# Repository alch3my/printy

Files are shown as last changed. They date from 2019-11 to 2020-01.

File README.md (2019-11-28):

# Printy

Printy is an Open Source SLA 3D printer. 
Visit us at www.alch3my.com

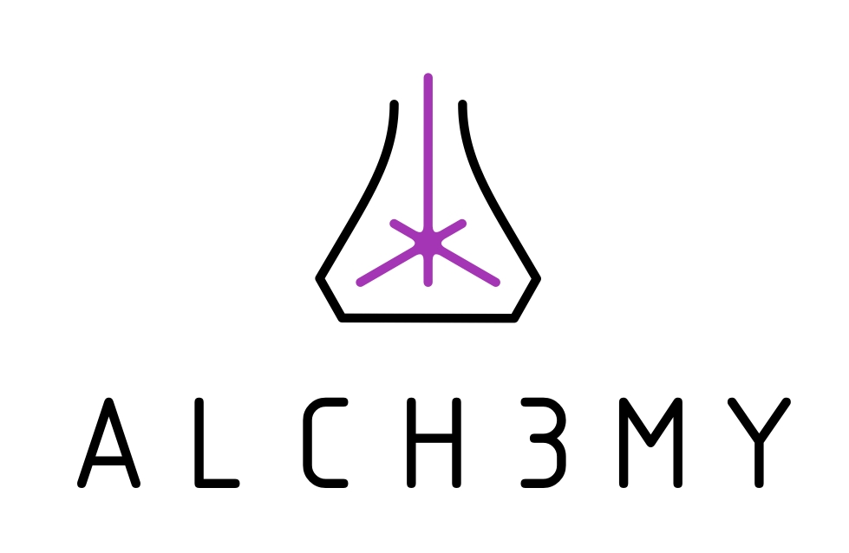
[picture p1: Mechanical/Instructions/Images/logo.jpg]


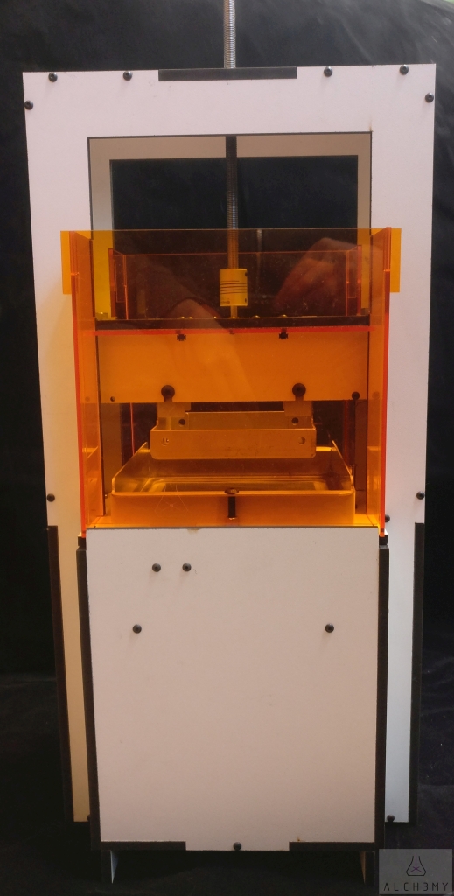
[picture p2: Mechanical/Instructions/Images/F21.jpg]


## Description
Alch3my is an open-source initiative for making the latest 3D printing technology accessible to everyone. Printy is an open-source SLA printer. We aim to democratize SLA technology with this fun and easy to build kit. Assembly takes 4 hours.

## Sourcing the Components
### Option 1: Everything from Alch3my
Purchase a complete kit. This takes all the work out of qualifying and sourcing. This option is perfect for a weekend project.
### Option 2: Only the Essentials
Do you have access to a laser cutter? Do you already have Arduino Mega, NEMA17 motor, stepper board, switches, etc from other projects? We will provide an essentials kit that includes Alch3my created hardware: the ResinShield and the aluminum sheet metal pieces. Download bill of materials and all the laser cutting DXF files from our website or GitHub account.
### Option 3: From Scratch
Are you a hard core maker? Do you like to make, improve, and redistribute hardware? We will provide schematics, gerbers, firmware, CAD files and documentation at Alch3my.com or our GitHub page so you can base your next design on ours. Please observe the license and give credit to Alch3my.

## [Build Instructions](./Mechanical/Instructions/BuildInstructions.md)

## [Software Installation](http://www.alch3my.com)

## [Calibration](http://www.alch3my.com)

Plans published by Alch3my LLC.

CERN OHL v1.2 license whenever appliable.

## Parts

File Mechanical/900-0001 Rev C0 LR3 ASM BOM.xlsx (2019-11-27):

Main Product
Item # | Name | Quantity | Comment | Part # | Supplier | Additional Info
1 | Laser cut pieces | 1 |  | 200-0001 Rev C0 | Ponoko
2 | Aluminum print bed | 1 | With 95185A640 pressed | 201-0001 Rev C
3 | Resinshield | 1 | Contact Alice (alice-yi@elecrow.com) | 101-0001 Rev G | Elecrow | reference number 104645
4 | Laser | 1 | 405nm 50mW, without driver, contact Merry Young (sales@laserland.com) | 3350 405nm 50mW | laserland.com |  | https://store.laserland.com/diode-laser-module/405nm/405dot/3350-405d.html
5 | Galvo + driver | 1 | HT-15K
6 | Stepper driver | 1 | Common open source part (A4988), must have heatsink
7 | Arduino Mega | 1 | Common open source part, any equivalent will work
8 | endstop switch | 3 | Common open source part, any equivalent will work
9 | 12v 3A regulated wall supply | 1 | arduino size barrel
10 | 3 pin JST cable | 1 | Source from galvo manufacturer
11 | 3 pin power cable | 1 | Source from galvo manufacturer
12 | Aluminum resevoir | 1 |  | 201-0002 Rev A3
13 | FEP film | 1 | 5mil thick, 8inx8in, also source from CS Hyde | 85905K66 |  | https://www.mcmaster.com/85905k66
14 | NEMA17 | 1 | 1.5A, 1M cable, 1.8deg, 0.1in female connector for headers
15 | Fastener Kit | 1 |  | 202-0001 Rev C
16 | Mechanical Kit | 1 |  | 202-0002 Rev A
17 | Misc Kit | 1 |  | 202-0003 Rev C
Misc Kit | 202-0003 Rev C
Item # | Name | Quantity | Comment | Part # | Supplier | Additional Info
1 | Adhesive zip tie mount | 4 | Higher quantity package is OK if cheaper |  |  | https://www.mcmaster.com/7566k25
2 | Double sided tape | 1 | 3M VHB RP32, 0.75in width, >= 36inch cut strip or roll | RP32 | 3M
3 | Zip tie | 10 | 0.1" wide >= 3" long. Higher quantity package is OK if cheaper | 7130K12 | mcmaster | https://www.mcmaster.com/7130k12
4 | Wire loom | 1 | 2ft
5 | Laser safety goggles | 1 | Must block 405nm
6 | Single sided tape | 1 | Polyester tape, 3M 1318-1 or equivalent, 0.75in width, >= 36in strip or roll |  | 3M
7 | Metric allen wrench set | 1 | Must include M2, M2.5, M3. Keep cost <$0.50
Mechanical | 202-0002 Rev A |  | Try to source all from the same vendor
Item # | Name | Quantity | Comment | Part # | Supplier | Additional Info
1 | ACME T8x1 200mm with cart | 1 | T8, ACME, 1mm pitch, 200mm long, 8mm diameter, cart must have exact bolt pattern
2 | LMK8LUU | 2 | Pay attention to height, should be around 45mm
3 | SHF8 | 2
4 | Linear rail 8mm 300mm/12in | 2 | 8mm diameter, 300mm/12in long, pay attention to end machining
5 | 5mm to 8mm coupler | 1
Fasteners | 202-0001 Rev C
Item # | Name | Quantity | Comment | Part # | Supplier 1 | Additional Info
1 | M5x20 screw | 10 |  | 91239A233 | mcmaster | https://www.mcmaster.com/91239a233
2 | M4x10 screw | 3 |  | 91239A144 | mcmaster | https://www.mcmaster.com/#91239a144/=1502lqc
3 | M3 nut | 100 |  | 98676A100 | mcmaster | https://www.mcmaster.com/#98676a100/=1502cdh
4 | M3 brass press fit nut | 25 |  | 94510A240 | mcmaster | https://www.mcmaster.com/#94510a240/=1502d99
5 | M3x14 screw | 100 |  | 91239A118 | mcmaster | https://www.mcmaster.com/#91239A118
6 | M3x10 screw | 10 |  | 91239A115 | mcmaster | https://www.mcmaster.com/#91239a115/=1502ox1
7 | M3x16 screw | 8 |  | 91239A120 | mcmaster | https://www.mcmaster.com/#91239A120
8 | M3x50 screw | 1 |  | 92125A151 | mcmaster | https://www.mcmaster.com/92125a151
9 | M5 nut | 10 |  | 90592A095 | mcmaster | https://www.mcmaster.com/90592a095
10 | M5 standoff | 2 |  | 98952A141 | mcmaster | https://www.mcmaster.com/98952a141

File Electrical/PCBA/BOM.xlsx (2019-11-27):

 | RefDes | Name | Value | Description | Quantity | Pattern | Manufacturer | MPN
Fitted | C101, C102, C104, C108, C110, C113, C117, C118, C208, C209 | CAP_0805 | 10u | CAP CER 10UF 25V X5R 0805 | 10 | CAP_0805 |  | GRM21BR61E106KA73K | 96
Fitted | C103, C105, C112, C114, C115, C116, C202, C206, C207, C210, C301, C401 | CAP_0805 | 1u | CAP CER 1UF 35V X5R 0805 | 12 | CAP_0805 |  | GRM219R7YA105MA12D | 19
Fitted | C106, C109, C201, C203, C204, C205 | CAP_0603 | 100p | CAP CER 100PF 50V C0G/NP0 0603 | 6 | CAP_0603 |  | C0805C101J5GACTU
Fitted | C107, C111 | CAP_0603 | 6.8n | CAP CER 6800PF 50V C0G/NP0 0603 | 2 | CAP_0603 |  | CL21B682KBANNNC
Fitted | C302, C303 | CAP_1210 | 22u | CAP CER 22UF 16V X5R 1210 | 2 | CAP_1210 |  | CL32A226MOJNNNE
Not-fitted | C402, C502 | CAP_0805 | opt |  | 2 | CAP_0805
Not-fitted | C501 | CAP_1210 | opt |  | 1 | CAP_1210
Fitted | D101, D104 | PMEG4020ETP |  |  | 2 | SOD-128 | Nexperia | PMEG4020ETP,115
Fitted | D102, D103, D401 | APL3015SRCPRV-F01 |  |  | 3 | APL3015 | Kingbright | APL3015SRCPRV-F01
Not-fitted | D501, D502 | PMEG4020ETP | opt |  | 2 | SOD-128
Fitted | FB101, FB102, FB201, FB301 | BLM18KG221SN1D | 220 @ 100MHz |  | 4 | RES_0603 | Murata | BLM18KG221SN1D
Not-fitted | FD1, FD2, FD3 | Fiducial |  |  | 3 | Fiducial
Fitted | J1, J2, J4, J5, J7, J8 | 644456-8 |  |  | 6 | HDR-1x8T/2.54/20x2 | TE Connectivity | 3-644456-8
Fitted | J3 | 90131-0138 |  |  | 1 | HDR-2x18T/2.54x2.54/46x5 | Molex | 90131-0138
Not-fitted | J6, J9 | 90131-0125 | opt |  | 2 | HDR-2x5T/2.54x2.54/13x5 | Molex | 90131-0125
Not-fitted | J10, J203 | 644456-4 | opt |  | 2 | HDR-1x4T/2.54/10x2 | TE Connectivity | 61300411121
Fitted | J11, J12, J13, J301 | 644456-4 |  |  | 4 | HDR-1x4T/2.54/10x2
Fitted | J101 | 22272031 |  |  | 1 | Molex 3pin | Molex | 0022272031
Not-fitted | J201, J202 | B3B-XH-A | opt |  | 2 | JST B3B-XH-A | JST | B3B-XH-A(LF)(SN)
Fitted | J204 | B3B-XH-A |  |  | 1 | JST B3B-XH-A | JST | B3B-XH-A(LF)(SN)
Fitted | J302, J303 | PPTC081LFBN-RC |  |  | 2 | HDR-1x8T/2.54/20x2 | Sullins | PPTC081LFBN-RC
Fitted | J401, J402 | B2B-XH-A |  |  | 2 | JST B2B-XH-A | JST | B2B-XH-A(LF)(SN)
Not-fitted | J501 | OSTVN04A150 | opt |  | 1 | TB-1x4/2.54/11x7/Sc_H | On Shore | OSTVN04A150
Not-fitted | J502 | 644456-2 | opt |  | 1 | HDR-1x2T/2.54/5x2 | TE Connectivity | 3-644456-2
Fitted | Q401, Q402 | 2N7002 |  |  | 2 | SOT23 | Diodes | 2N7002-7-F
Not-fitted | Q501, Q502 | IRLZ44N | opt |  | 2 | TO-220 | Infineon | IRLZ44NPBF
Not-fitted | R1, R302, R304, R305, R306, R307, R501, R502, R503, R504, R505 | RES_0603 | opt |  | 11 | RES_0603
Fitted | R101, R115 | RES_1210 | 0 | RES SMD 0 OHM JUMPER 1/2W 1210 | 2 | RES_1210 |  | CRCW12100000Z0EA
Fitted | R102, R103, R108, R205, R210 | RES_0603 | 49k9 | RES SMD 49.9K OHM 1% 1/10W 0603 | 5 | RES_0603 |  | ERJ-3EKF4992V
Fitted | R104, R106, R112, R113, R202, R203, R204, R206, R207, R208, R209, R211, R401, R403 | RES_0603 | 100k | RES SMD 100K OHM 1% 1/10W 0603 | 14 | RES_0603 |  | AT0603FRE07100KL
Fitted | R105, R114 | RES_0603 | 464k | RES SMD 464K OHM 1% 1/10W 0603 | 2 | RES_0603 |  | RC0603FR-07464KL
Fitted | R107, R111, R402 | RES_0603 | 24k9 | RES SMD 24.9K OHM 1% 1/10W 0603 | 3 | RES_0603 |  | ERJ-3EKF2492V
Fitted | R109, R405 | RES_0603 | 6k04 | RES SMD 6.04K OHM 1% 1/10W 0603 | 2 | RES_0603 |  | ERJ-3EKF6041V
Fitted | R110 | RES_0603 | 53k6 | RES SMD 53.6K OHM 1% 1/10W 0603 | 1 | RES_0603 |  | RC0603FR-0753K6L
Fitted | R201 | RES_0603 | 1k | RES SMD 1K OHM 1% 1/10W 0603 | 1 | RES_0603 |  | ERJ-3EKF1001V
Fitted | R212, R213 | RES_0603 | 24r9 | RES SMD 24.9 OHM 1% 1/10W 0603 | 2 | RES_0603 |  | ERJ-3EKF24R9V
Fitted | R301, R303 | RES_0603 | 0 | RES SMD 0 OHM JUMPER 1/10W 0603 | 2 | RES_0603 |  | ERJ-3GEY0R00V
Fitted | R407 | RES_0603 | 18r2 | RES SMD 18.2 OHM 1% 1/10W 0603 | 1 | RES_0603 |  | ERJ-3EKF18R2V
Fitted | T101, T102 | SRF1260-150M | 15uH |  | 2 | SRF1260 | Bourns | SRF1260-150M
Not-fitted | TP101, TP102, TP103, TP201, TP202, TP203, TP204, TP205, TP206, TP207, TP208, TP501, TP502, TP503 | TESTPOINT |  |  | 14 | Round
Fitted | U101 | LT8582 |  |  | 1 | 4x7DFN | Linear Technology | LT8582EDKD#PBF
Fitted | U102 | NCP1117ST50T3G |  |  | 1 | SOT223-4 | ON Semi | NCP1117ST50T3G
Fitted | U201 | LM4040DIM3-4.1 |  |  | 1 | SOT23 | Texas Instruments | LM4040DIM3-4.1/NOPB
Fitted | U202 | TL084D |  |  | 1 | SOIC-14/150mil | Texas Instruments | TL084CDR
Fitted | U203 | LTC2602CMS8 |  |  | 1 | MSOP-8 | Linear Technology | LTC2622CMS8#PBF
Fitted | U401 | LM321MF |  |  | 1 | SOT23-5 | Texas Instruments | LM321MF/NOPB
Not-fitted | X1 | Arduino Mega |  |  | 1
Not-fitted | X301 | A4988 Carrier |  |  | 1

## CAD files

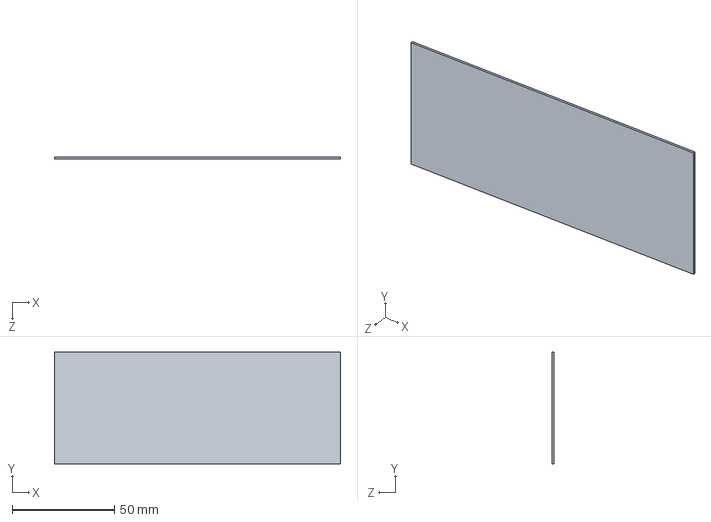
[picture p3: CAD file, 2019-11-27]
Electrical/PCBA/resinshield.step
139.7 x 54.6 x 0.991 mm

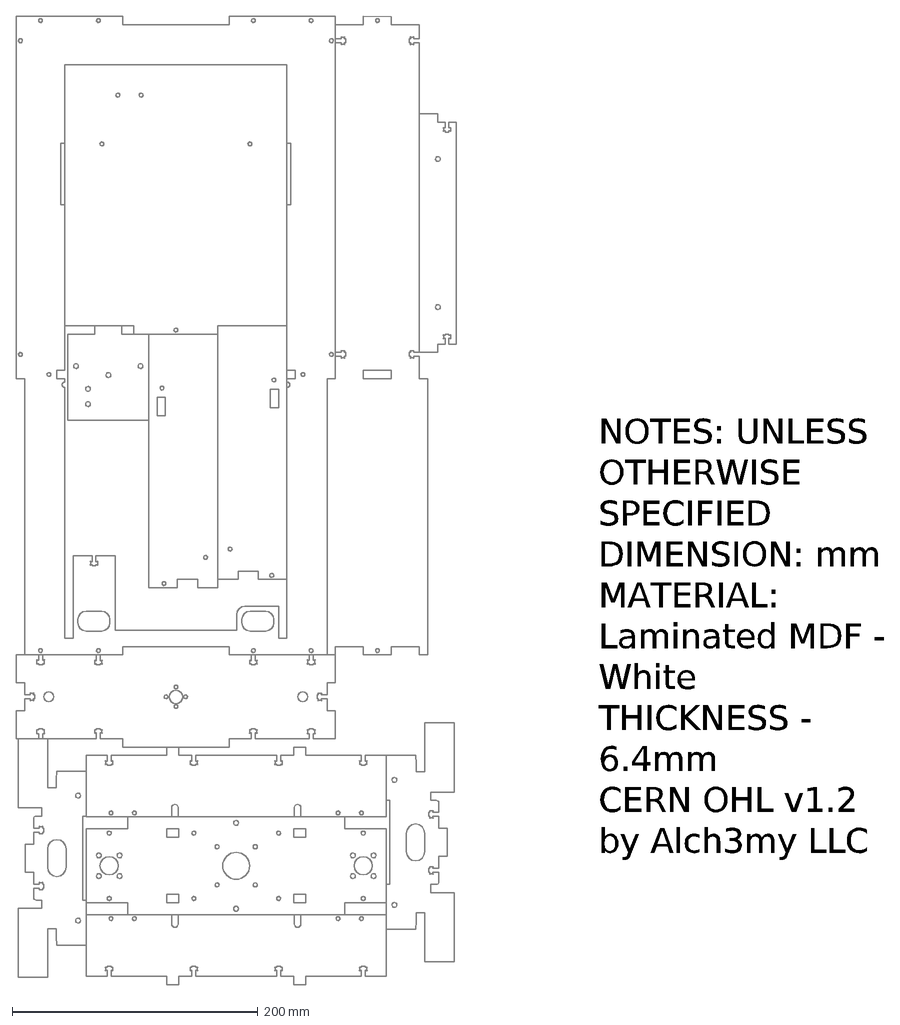
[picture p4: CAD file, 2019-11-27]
Mechanical/200-0001 Laser Cut/wood2_p3.dxf
NOTES: UNLESS OTHERWISE SPECIFIED DIMENSION: mm MATERIAL: Laminated MDF - White THICKNESS - 6.4mm CERN OHL v1.2 by Alch3my LLC

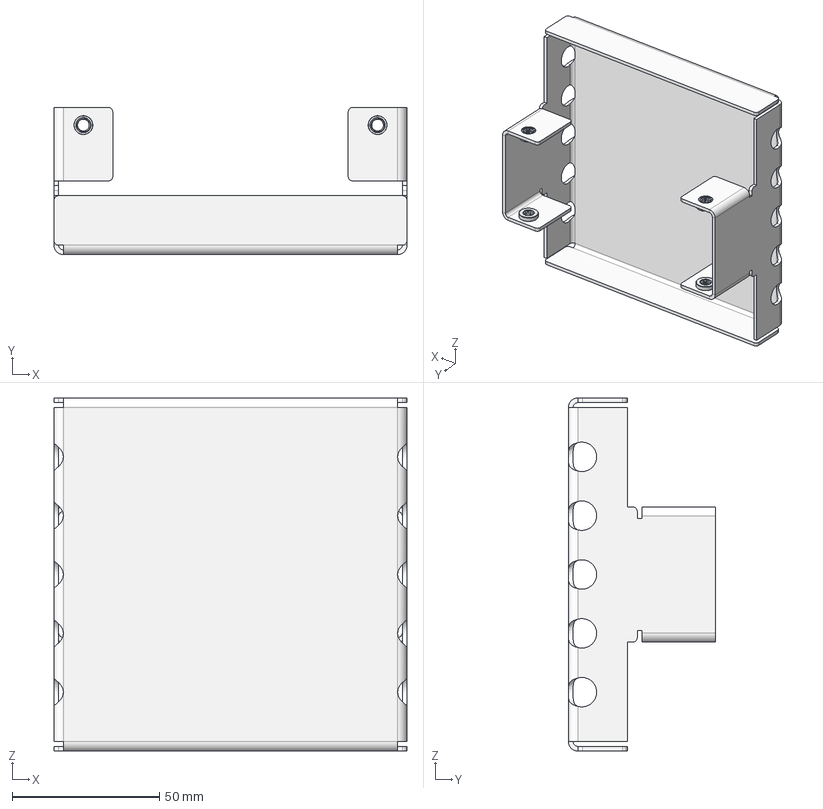
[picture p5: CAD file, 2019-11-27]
Mechanical/201-0001 BedSM/201-0001 Rev C bedsm.stp
120.0 x 50.0 x 120.0 mm
bedsm
95185A640_ZINC-PLTD STL PRESS-FIT NUT FOR SHEET METAL x 4

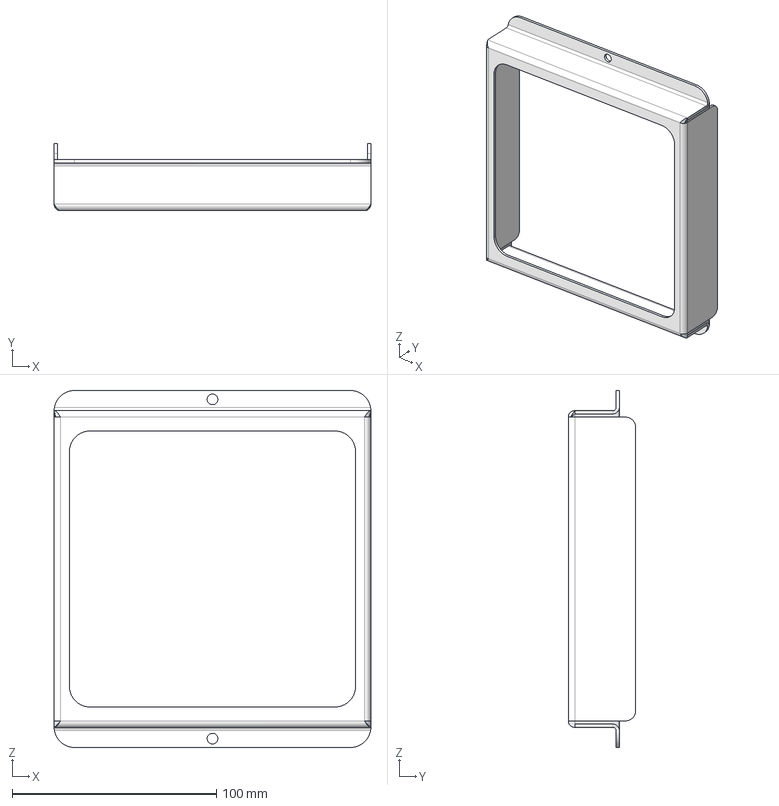
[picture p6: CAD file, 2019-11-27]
Mechanical/201-0002 ReservoirSM/201-0002 Rev A3 reservoirsm.stp
155.0 x 33.0 x 174.7 mm
reservoirsm_weldment_1
reservoirsm

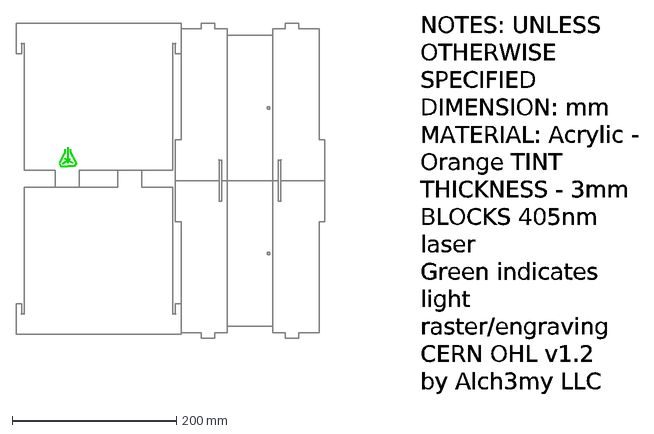
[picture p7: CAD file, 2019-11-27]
Mechanical/200-0001 Laser Cut/clear_orange_p2.dxf
NOTES: UNLESS OTHERWISE SPECIFIED DIMENSION: mm MATERIAL: Acrylic - Orange TINT THICKNESS - 3mm BLOCKS 405nm laser Green indicates light raster/engraving CERN O

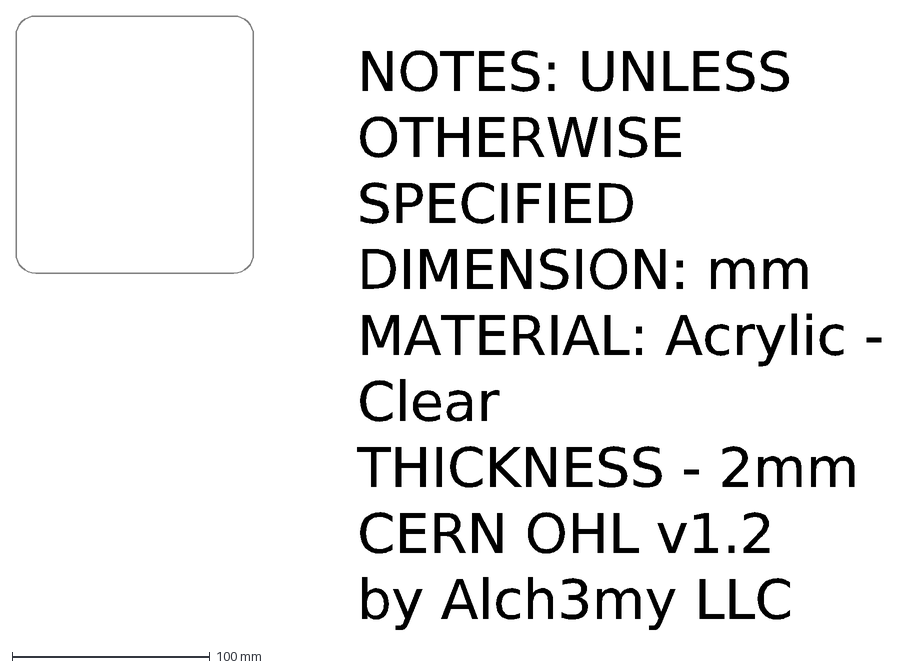
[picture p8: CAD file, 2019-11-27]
Mechanical/200-0001 Laser Cut/clear_acrylic_p1.dxf
NOTES: UNLESS OTHERWISE SPECIFIED DIMENSION: mm MATERIAL: Acrylic - Clear THICKNESS - 2mm CERN OHL v1.2 by Alch3my LLC

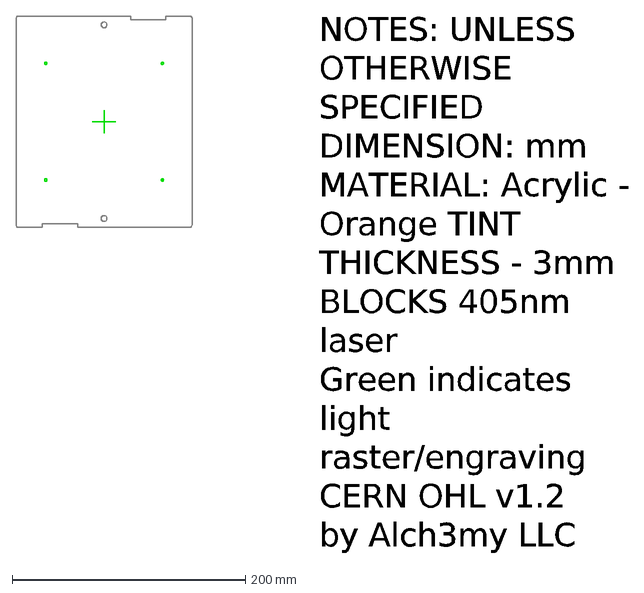
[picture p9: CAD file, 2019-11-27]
Mechanical/200-0001 Laser Cut/clear_orange_p1.dxf
NOTES: UNLESS OTHERWISE SPECIFIED DIMENSION: mm MATERIAL: Acrylic - Orange TINT THICKNESS - 3mm BLOCKS 405nm laser Green indicates light raster/engraving CERN O

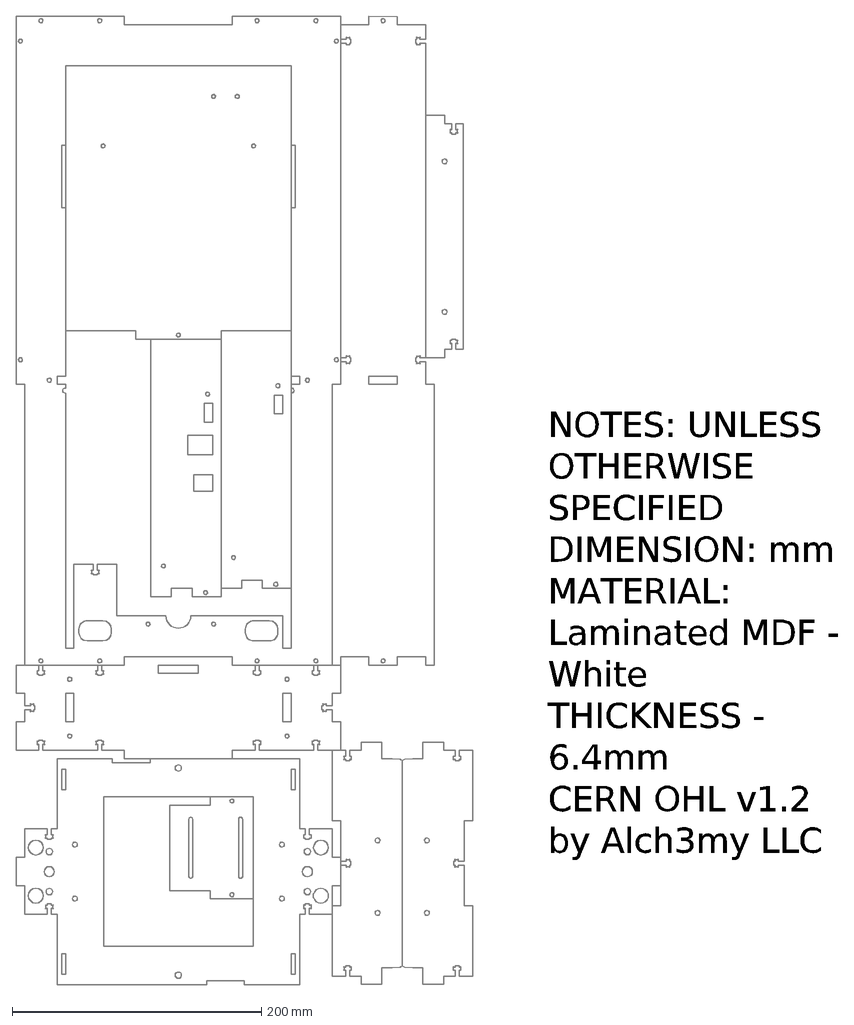
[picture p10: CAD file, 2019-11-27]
Mechanical/200-0001 Laser Cut/wood1_p3.dxf
NOTES: UNLESS OTHERWISE SPECIFIED DIMENSION: mm MATERIAL: Laminated MDF - White THICKNESS - 6.4mm CERN OHL v1.2 by Alch3my LLC

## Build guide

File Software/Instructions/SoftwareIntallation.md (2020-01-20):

# Printy

Printy is an Open Source SLA 3D printer. 
Visit us at www.alch3my.com





## Description
Alch3my is an open-source initiative for making the latest 3D printing technology accessible to everyone. Printy is an open-source SLA printer. We aim to democratize SLA technology with this fun and easy to build kit. Assembly takes 4 hours.

## Software Installation
### Arduino IDE
Get the latest Arduino IDE from https://www.arduino.cc/en/main/software and install.

### Printy Firmware
Get the latest Printy firmware from https://github.com/alch3my/printy/tree/master/Software/Firmware

Connect an Arduino Mega or equivalent microcontroller board via USB to your computer.



Figure F1. Connect Arduino Mega

Load the firmware project "Marlin.ino" into the Arduino IDE

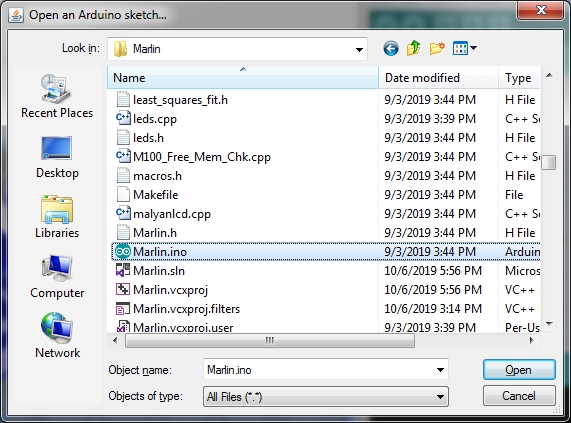
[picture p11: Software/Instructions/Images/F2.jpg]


Figure F2. Load Firmware

Ensure the "board", "processor", and "port" options reflect the connected Arduino Mega or equivalent. Press upload.

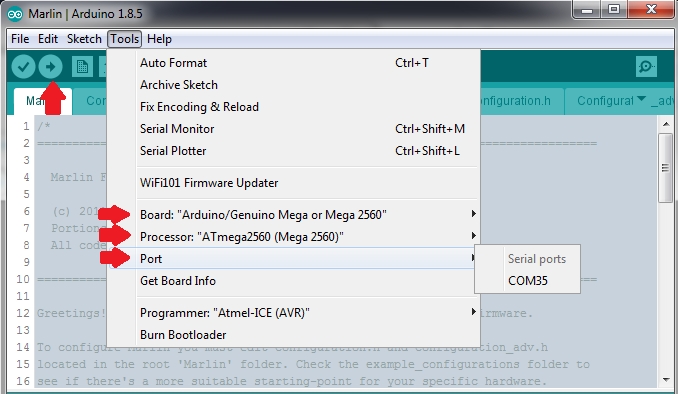
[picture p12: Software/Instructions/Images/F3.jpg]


Figure F3. Arduino IDE Configuration and Upload

Exit Arduino IDE once the upload is successful.

### Repetier Host
Get Repetier Host from https://www.repetier.com and install.

Use the following settings in "Printer Settings" to setup Printy.

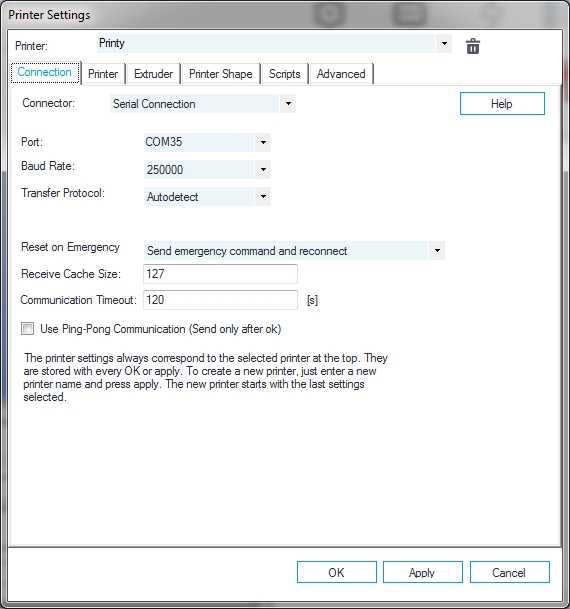
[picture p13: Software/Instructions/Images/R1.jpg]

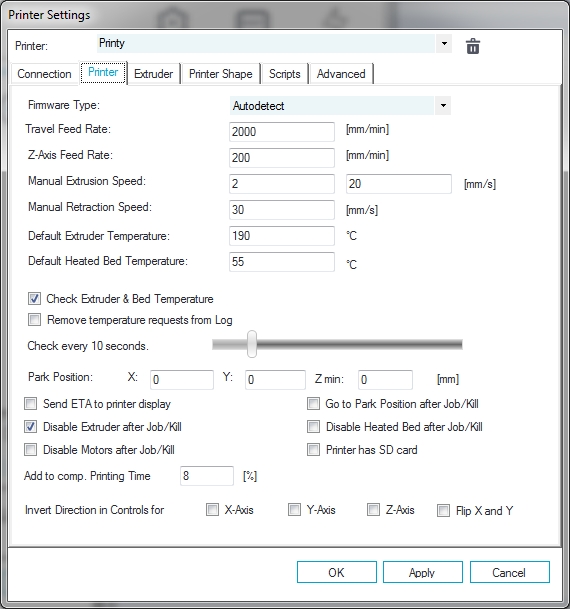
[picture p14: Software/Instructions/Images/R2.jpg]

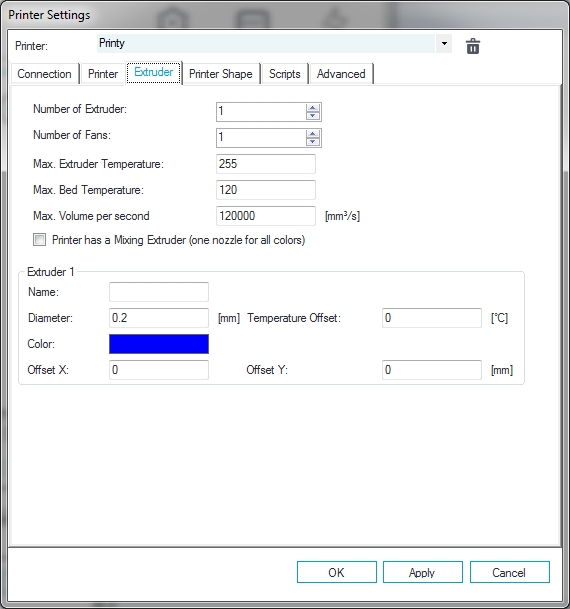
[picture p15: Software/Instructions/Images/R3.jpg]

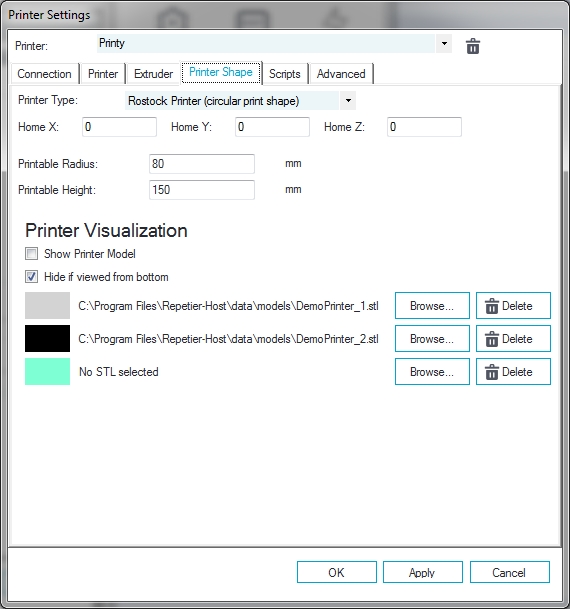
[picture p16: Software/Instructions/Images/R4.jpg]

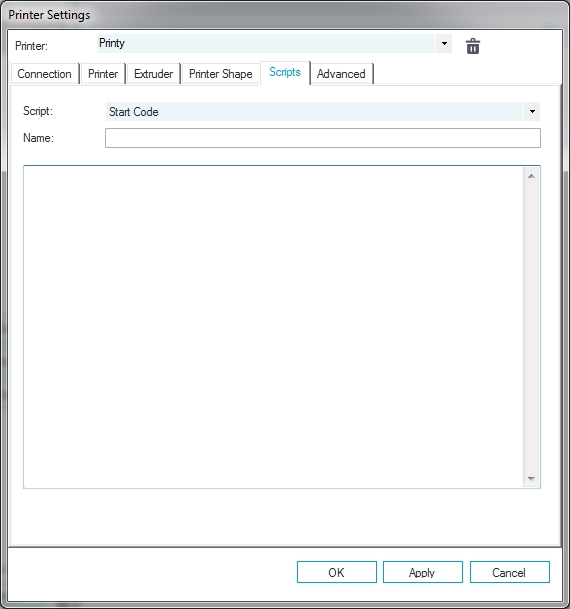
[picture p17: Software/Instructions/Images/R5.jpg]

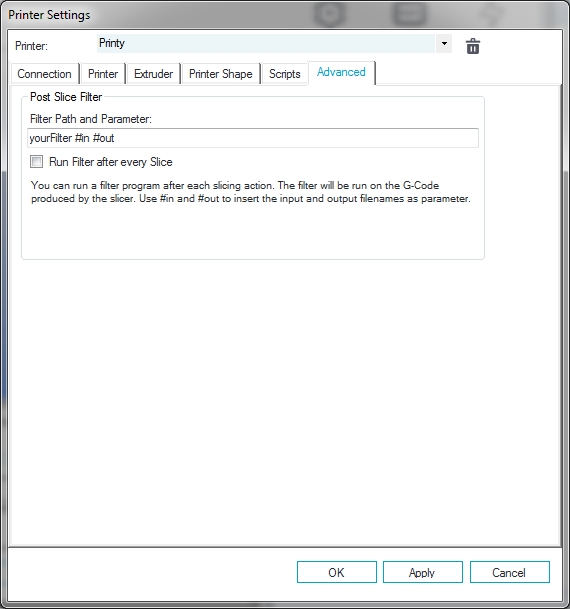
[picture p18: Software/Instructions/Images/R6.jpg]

Figures R1-6. Printer Settings

Note the "Port Number" should be the one your computer assign to the connected Arduino Mega or equivalent microcontroller.

### Slic3r Settings

Slic3r is a slicing tool typically used in FDM printers. Printy mimics the operation of an FDM by steering a laser beam across the print surface. Use the following settings to setup Slic3r. These settings will need to be tweaked for specific resins. Maker Juice G+ was extensively tested with these settings.

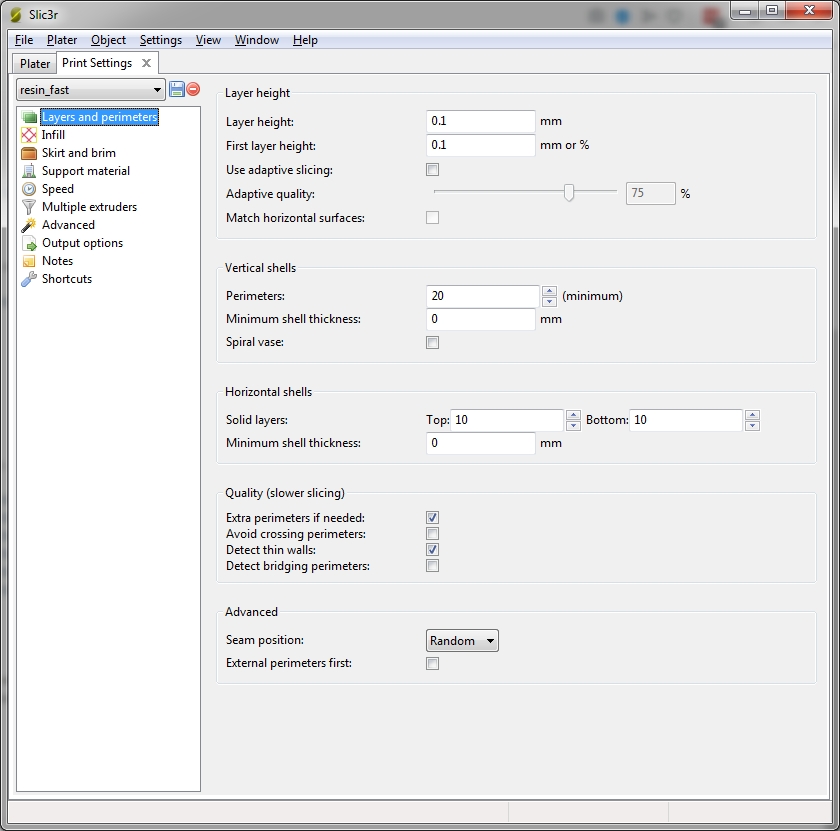
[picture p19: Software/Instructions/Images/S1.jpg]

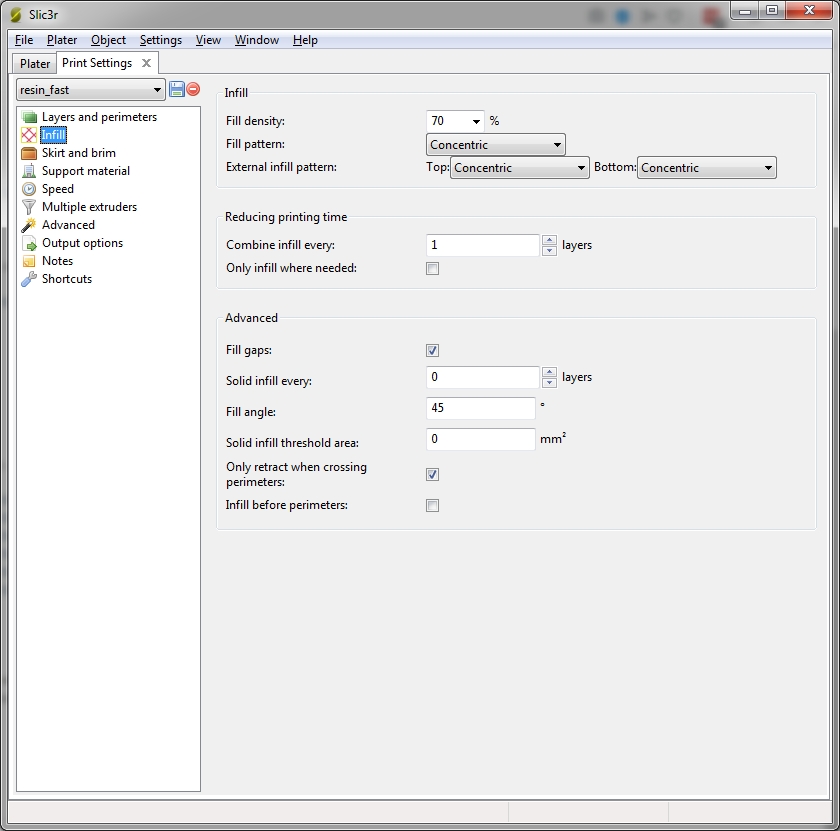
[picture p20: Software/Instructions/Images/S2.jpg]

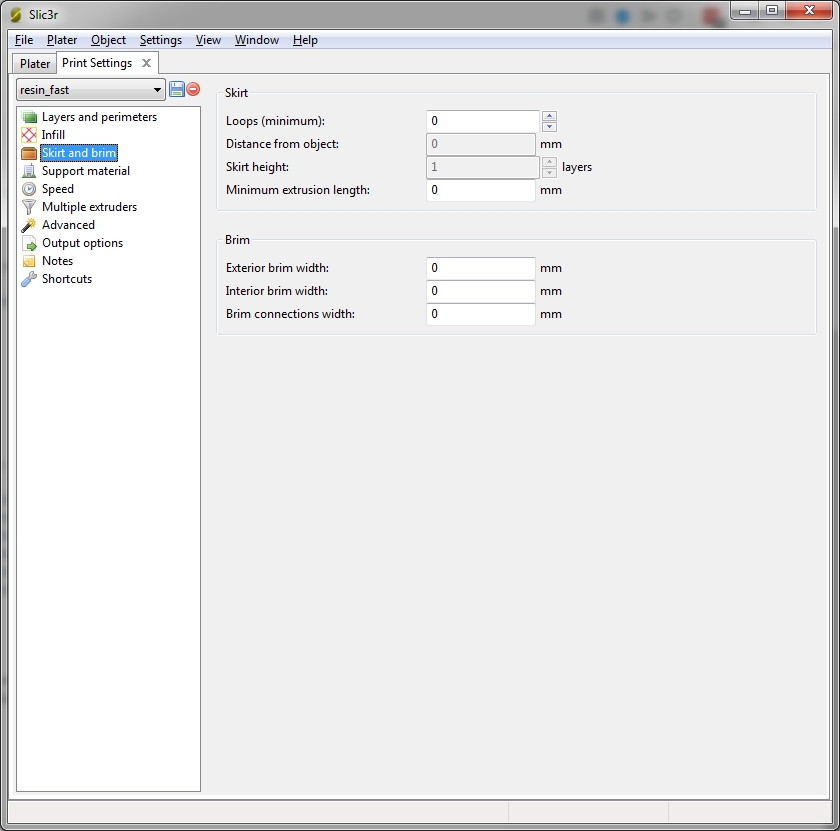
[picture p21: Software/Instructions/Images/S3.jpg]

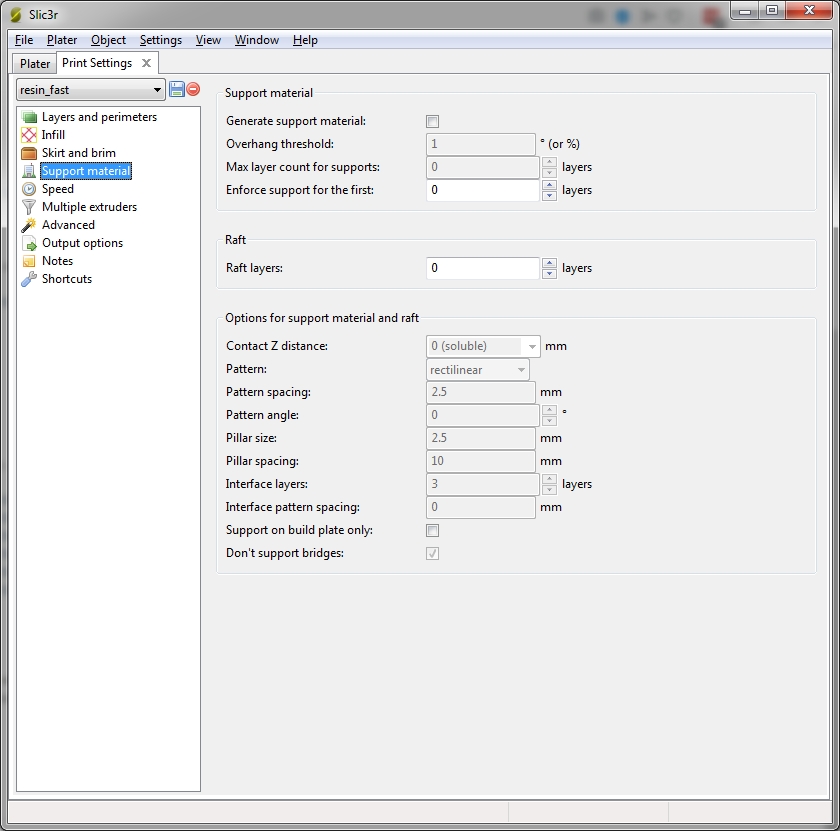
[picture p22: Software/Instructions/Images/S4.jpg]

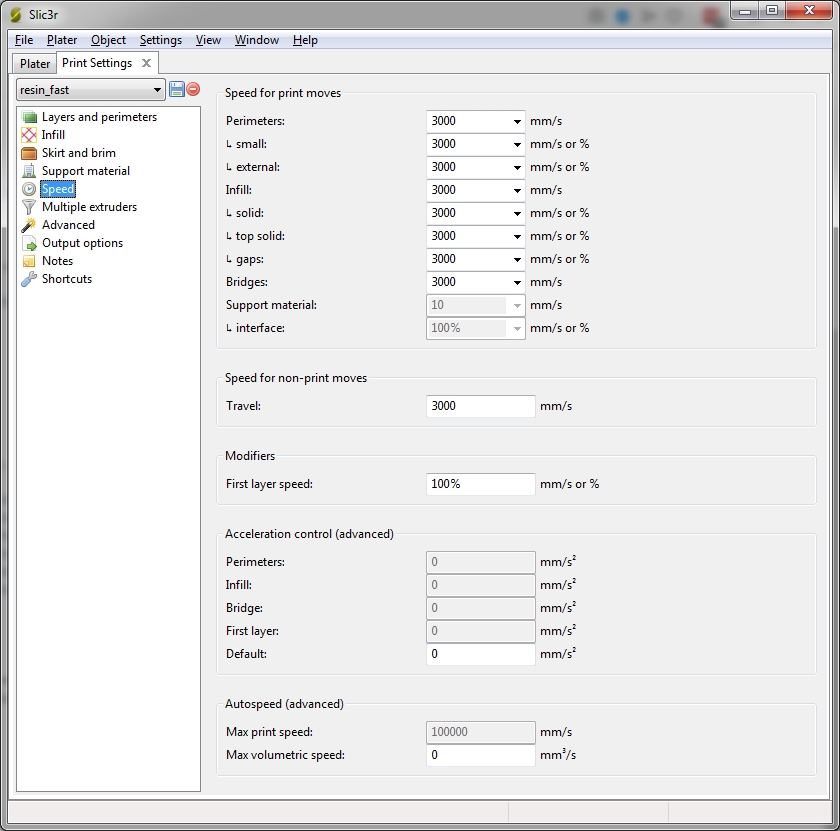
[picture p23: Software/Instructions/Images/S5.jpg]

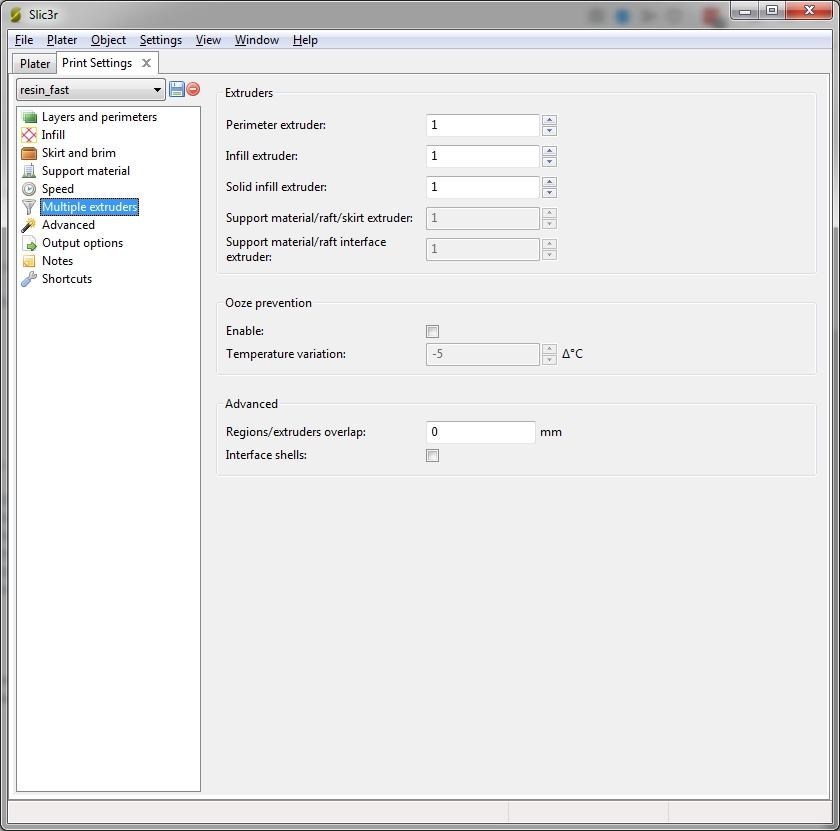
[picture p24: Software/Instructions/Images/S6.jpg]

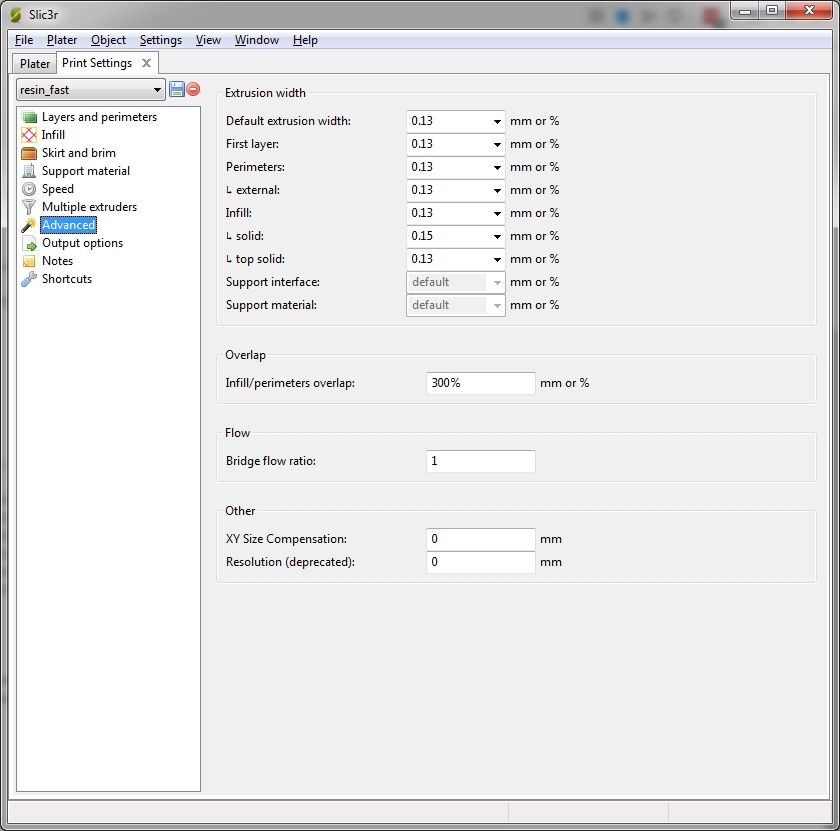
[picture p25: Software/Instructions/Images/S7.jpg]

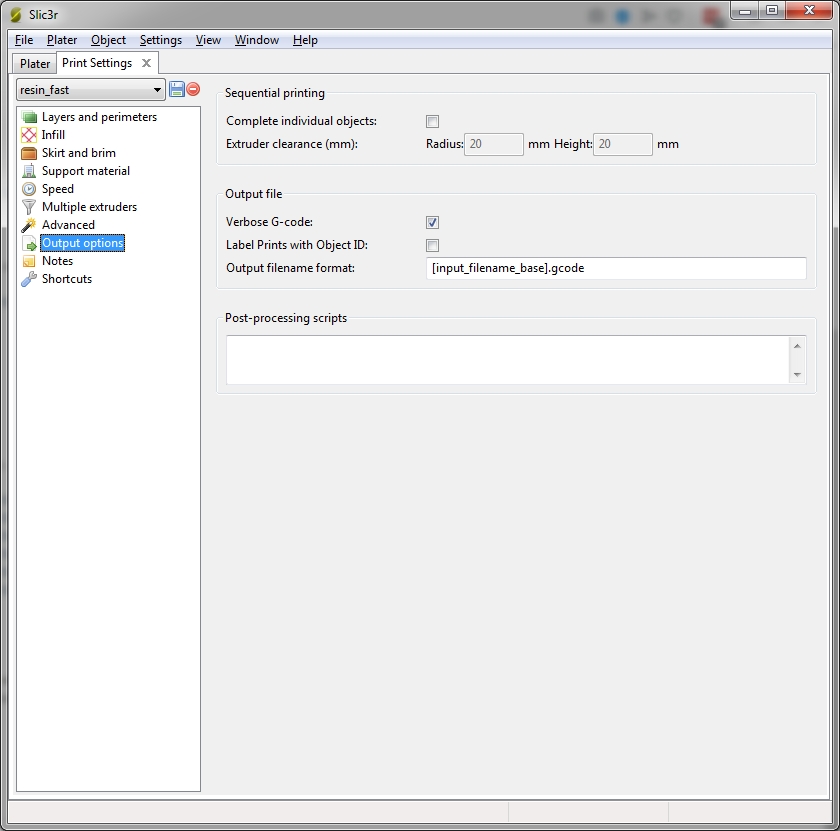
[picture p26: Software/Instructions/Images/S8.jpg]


Figures S1-8. Slic3r Print Setting

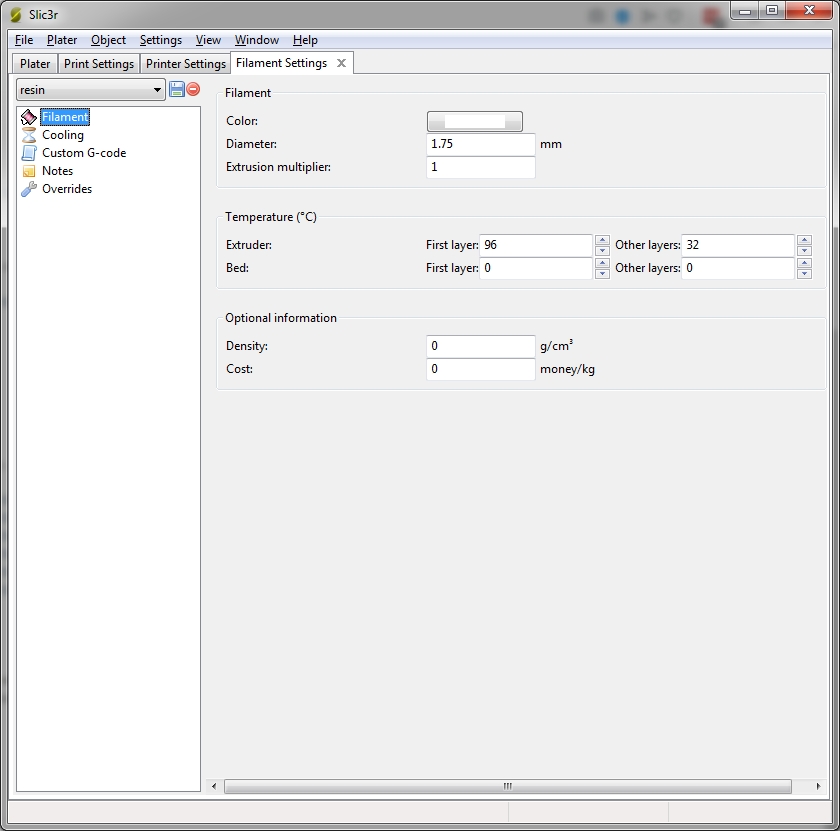
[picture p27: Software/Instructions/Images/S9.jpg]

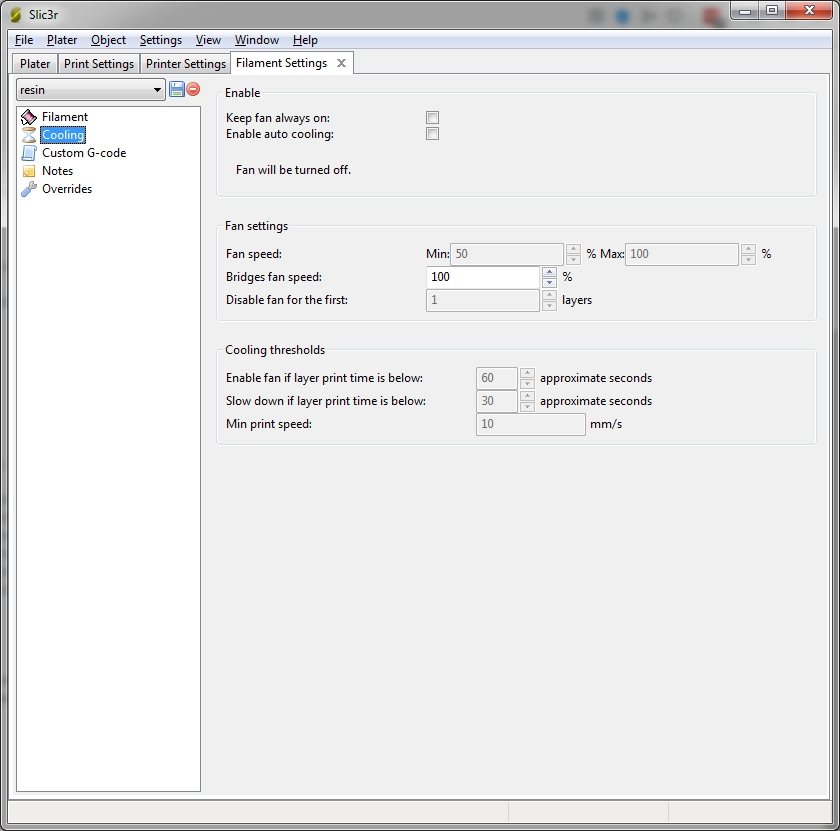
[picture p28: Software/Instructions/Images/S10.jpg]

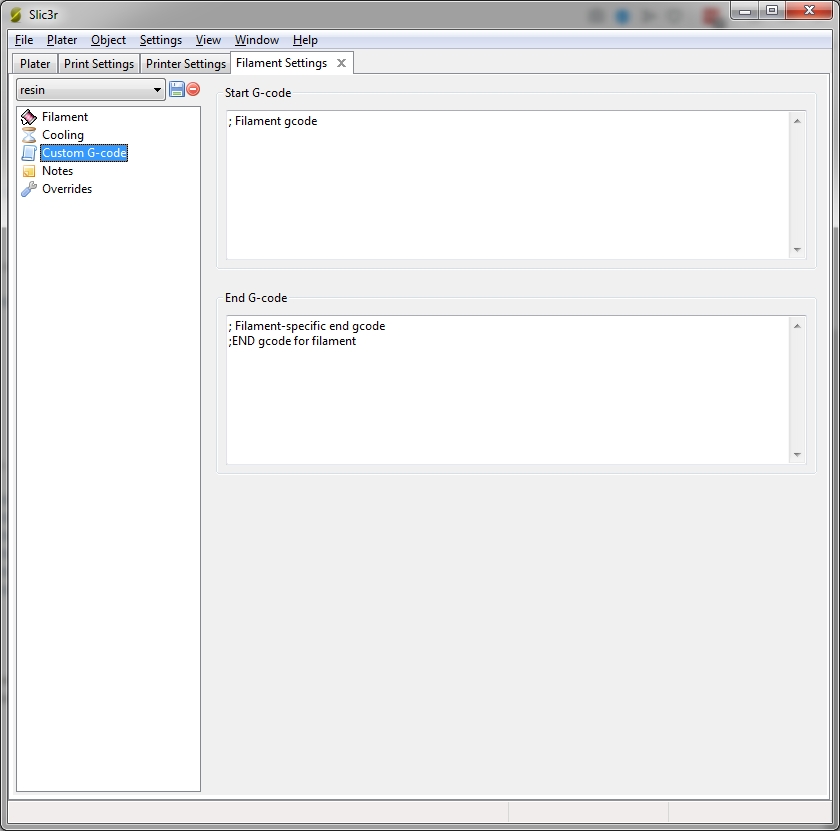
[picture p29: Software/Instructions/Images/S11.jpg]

Figures S9-11. Slic3r Filament Setting

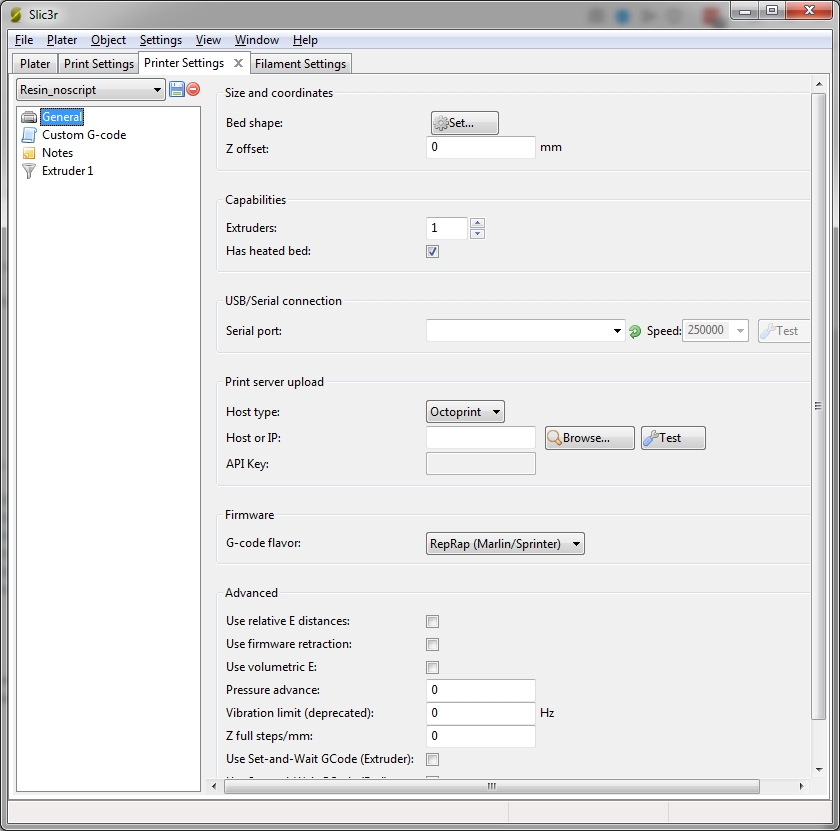
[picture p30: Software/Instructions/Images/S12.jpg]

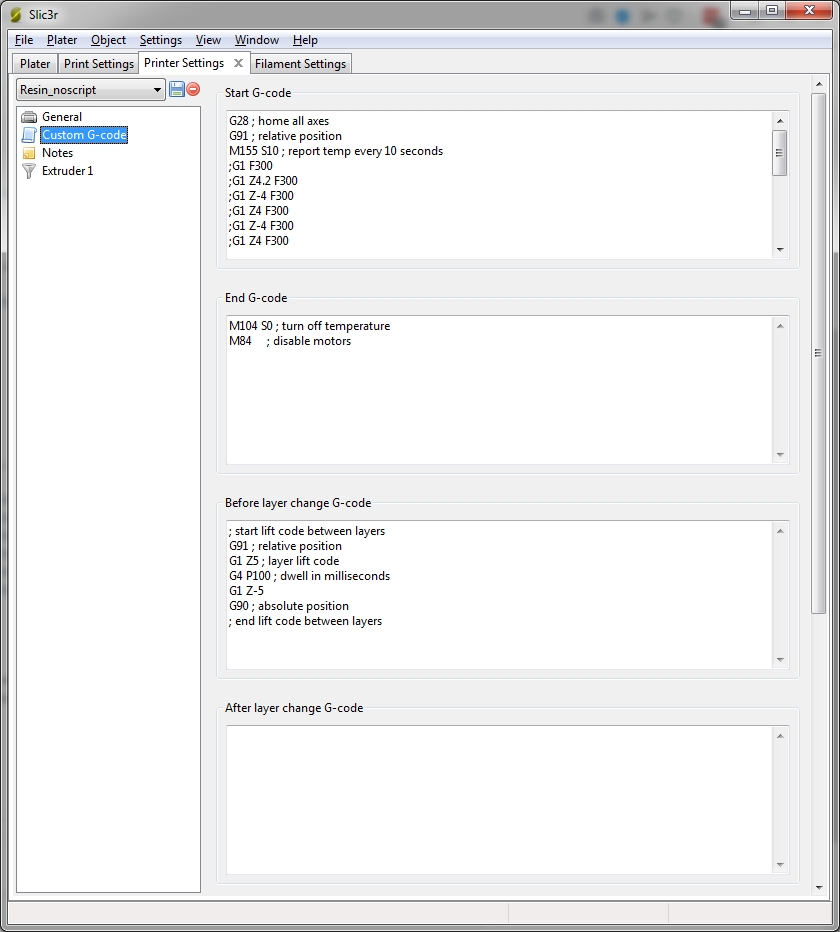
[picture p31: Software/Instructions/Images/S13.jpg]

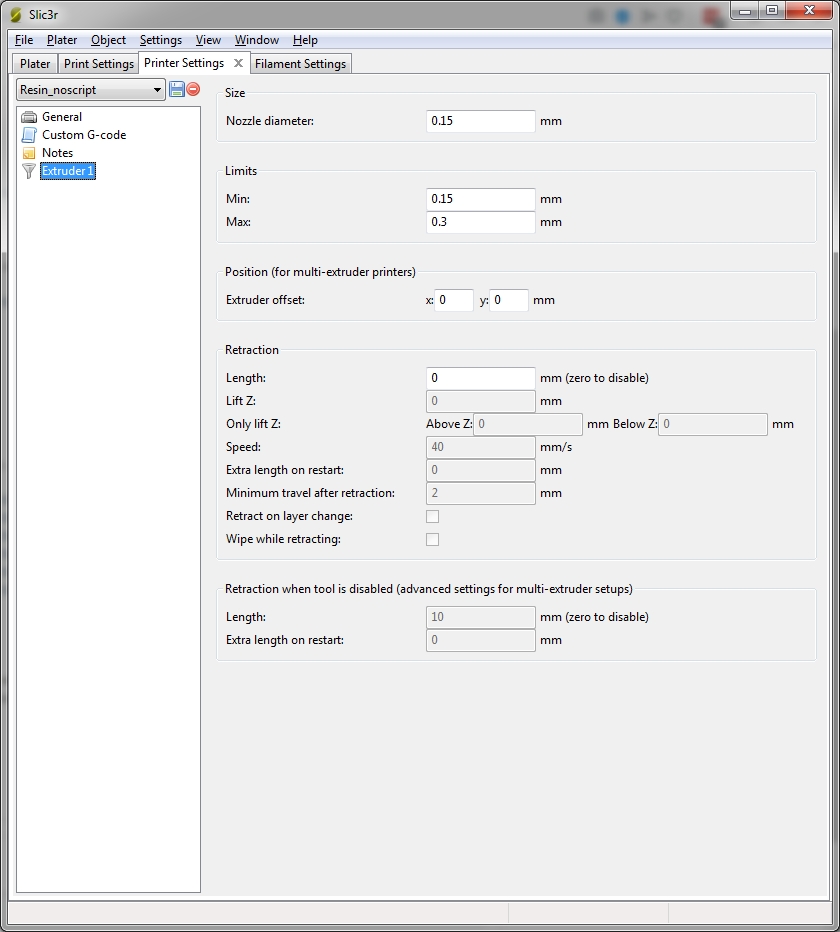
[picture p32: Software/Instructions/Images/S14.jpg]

Figures S12-14. Slic3r Printer Setting

Use the following "Start G-Code" in "Slic3r Printer Setting":

~~~~
G28 ; home all axes
G91 ; relative position
M155 S10 ; report temp every 10 seconds
G1 F300
G1 Z4.2 F300
G1 Z-4 F300
G1 Z4 F300
G1 Z-4 F300
G1 Z4 F300
G1 Z-4 F300
G1 Z4 F300
G1 Z-4 F300
G1 Z4 F300
G1 Z-4.1 F300
G1 Z10 F300
G1 Z-10 F20
G90 ; absolute position
G4 P1000 ; dwell in milliseconds
; end initial lift code
~~~~

Use the following "End G-Code":
~~~~
M104 S0 ; turn off temperature
M84     ; disable motors
~~~~

Use the following "Before Layer Change G-Code":
~~~~
; start lift code between layers
G91 ; relative position
G1 Z5 ; layer lift code
G4 P100 ; dwell in milliseconds
G1 Z-5
G90 ; absolute position
; end lift code between layers
~~~~

### Published by Alch3my LLC 

### CERN OHL v1.2 license whenever applicable.

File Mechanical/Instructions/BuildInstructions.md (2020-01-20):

# Printy Build Instructions





## Description
Alch3my is an open-source initiative for making the latest 3D printing technology accessible to everyone. Printy is an open-source SLA printer. We aim to democratize SLA technology with this fun and easy to build kit. Assembly takes 4 hours.

## Sourcing the Components
### Option 1: Everything from Alch3my
Purchase a complete kit. This takes all the work out of qualifying and sourcing. This option is perfect for a weekend project.
### Option 2: Only the Essentials
Do you have access to a laser cutter? Do you already have Arduino Mega, NEMA17 motor, stepper board, switches, etc from other projects? We will provide an essentials kit that includes Alch3my created hardware: the ResinShield and the aluminum sheet metal pieces. Download bill of materials and all the laser cutting DXF files from our website or GitHub account.
### Option 3: From Scratch
Are you a hard core maker? Do you like to make, improve, and redistribute hardware? We will provide schematics, gerbers, firmware, CAD files and documentation at Alch3my.com or our GitHub page so you can base your next design on ours. Please observe the license and give credit to Alch3my.

## Build Instructions
### Overview
The Printy kit contains many laser cut pieces. Pay close attention to the orientation of pieces, since some of the pieces only fit together in the orientations described. All orientation directions assumes the printer is facing you. The __front__ is the side closest to you.; __left__ is on your left hand side, etc.
#### Setup
Begin by spreading all the pieces out for easy identification and to ensure you have all the necessary pieces. Please refer to the Bill of Materials (BOM).
#### Tools Needed
Metric Allen wrenchs including 2mm, 2.5mm, 3mm. A small wrench. Clear tape. Rough sand paper (20-40 grit).
#### Spares
Ample spare screws and nuts are shipped with the kit. If more are needed, refer to the BOM for hardware specifications.
#### Peel
Peel the protective tape from all laser cut pieces.

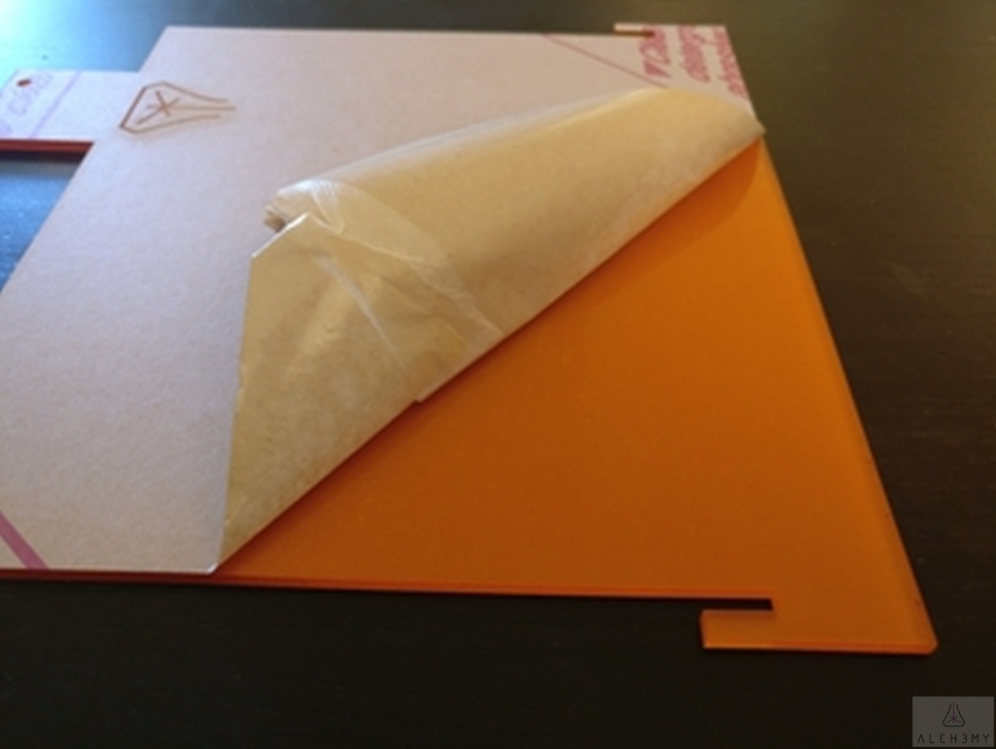
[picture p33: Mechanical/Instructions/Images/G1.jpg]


Figure G1. Peel the Protective Tape

#### T-Slot Joints
Printy is held together by T-slot joints. A bolt is inserted through one interface and a nut is inserted into a slot on the receiving end. __Do not overtighten!__

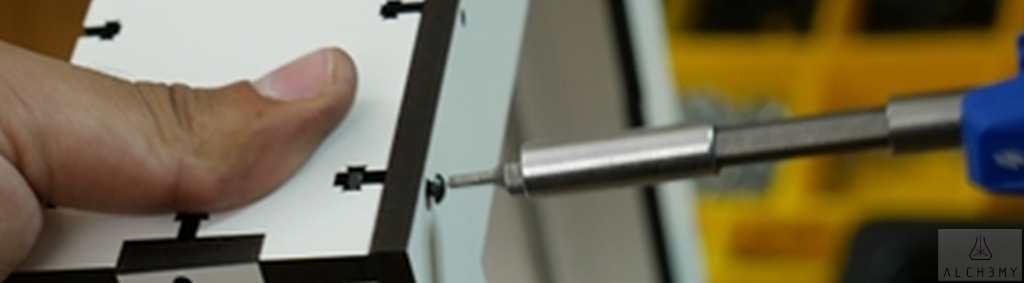
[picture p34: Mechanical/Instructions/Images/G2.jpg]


Figure G2. Proper Installation for T-Slot Joint

### Building the Crane
The crane holds the print platform, all holes are symmetric for your convenience. The two holes are for attaching the endstop switch, use the holes on the __front-right__.

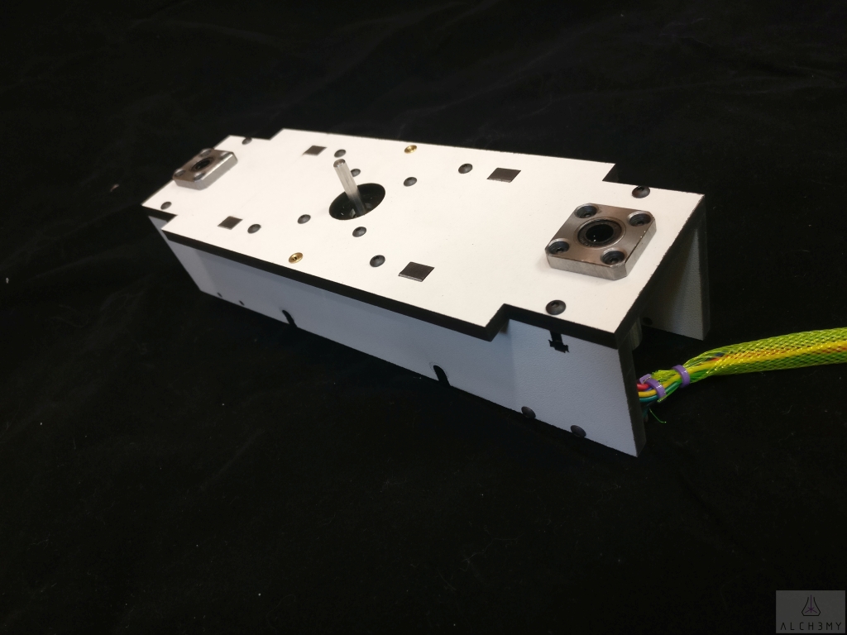
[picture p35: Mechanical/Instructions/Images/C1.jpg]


Figure C1. Assembly Orientation for the Crane

Attach the front and back piece of the crane to the top of the crane with 4 M3 nuts and 4 M3x14 screws each. A total of 8 M3 nuts and 8 M3x14 screws will be used.

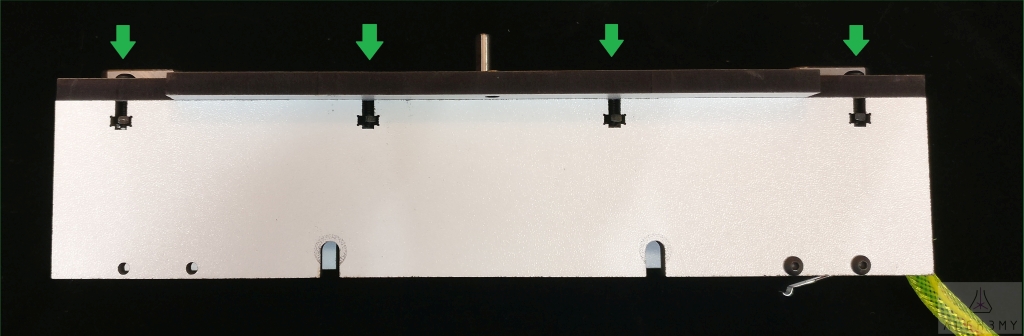
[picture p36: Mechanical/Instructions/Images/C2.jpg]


Figure C2. Assemble the Crane

Attach the NEMA17 motor to top of the crane with 4 M3x10 screws. Wires should come out on the __right__ side.

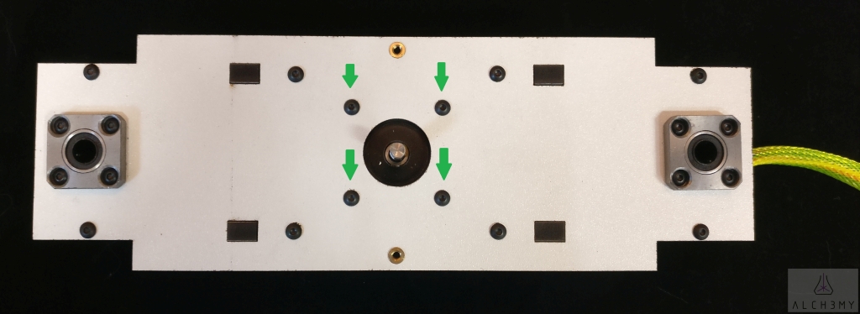
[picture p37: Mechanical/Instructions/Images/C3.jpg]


Figure C3. Install NEMA 17 Motor

Press in 8 M3 brass press-fit nuts into the crane from the __bottom__, 2 more from the __top__

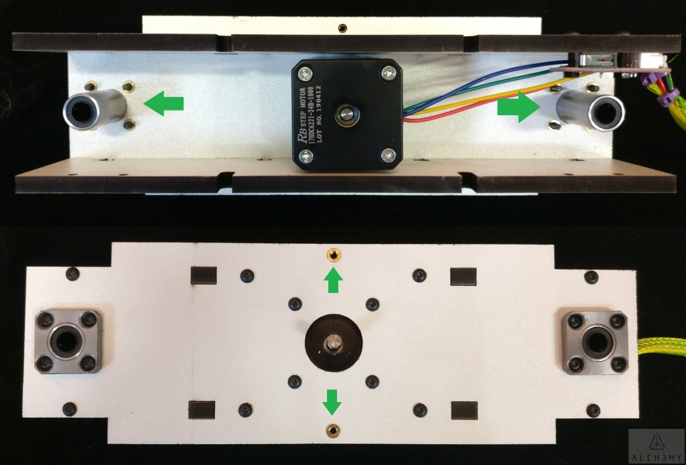
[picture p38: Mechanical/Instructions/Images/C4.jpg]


Figure C4. Brass Press-Fit Nuts

Insert the LMK8LUU bearings through top of the crane and attach with 4 M3x14 screws.

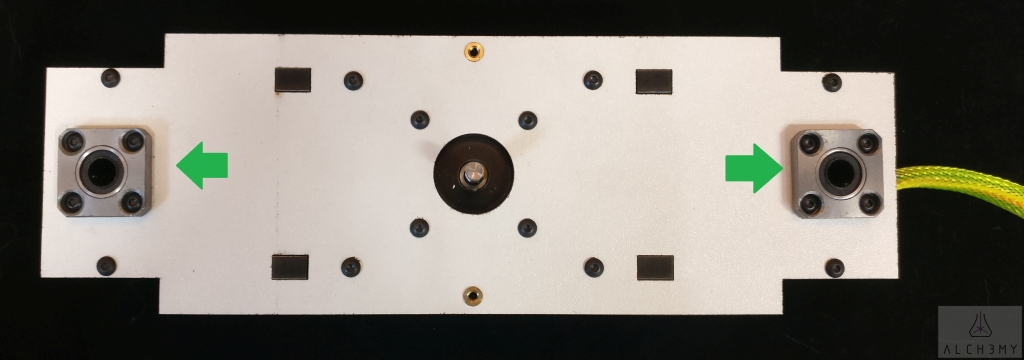
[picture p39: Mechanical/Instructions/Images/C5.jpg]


Figure C5. LMK8LUU Bearings

Attach the endstop switch with 2 M3x16 screw and 2 M3 nuts. The wires should points towards the __right__ side.

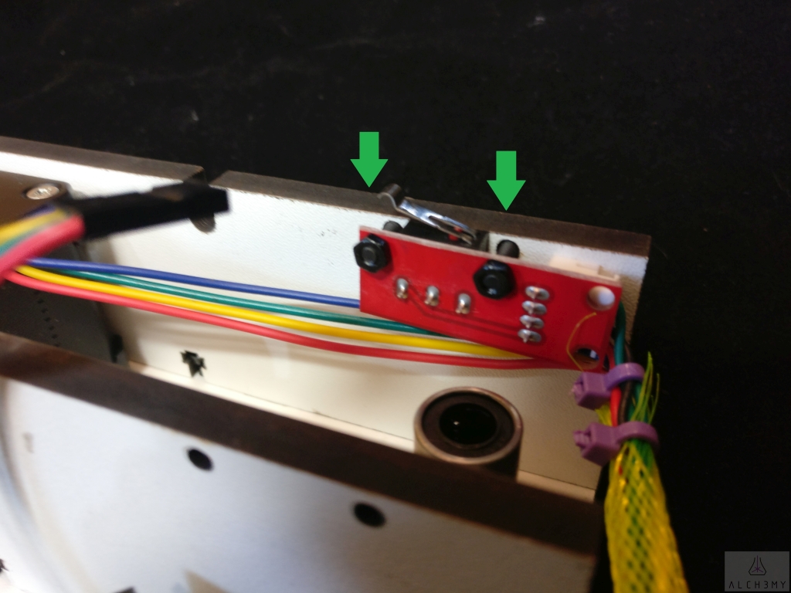
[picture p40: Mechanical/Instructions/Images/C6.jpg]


Figure C6. Endstop Switch

Enclose the motor and endstop wires in a sleeve, zip tie the ends

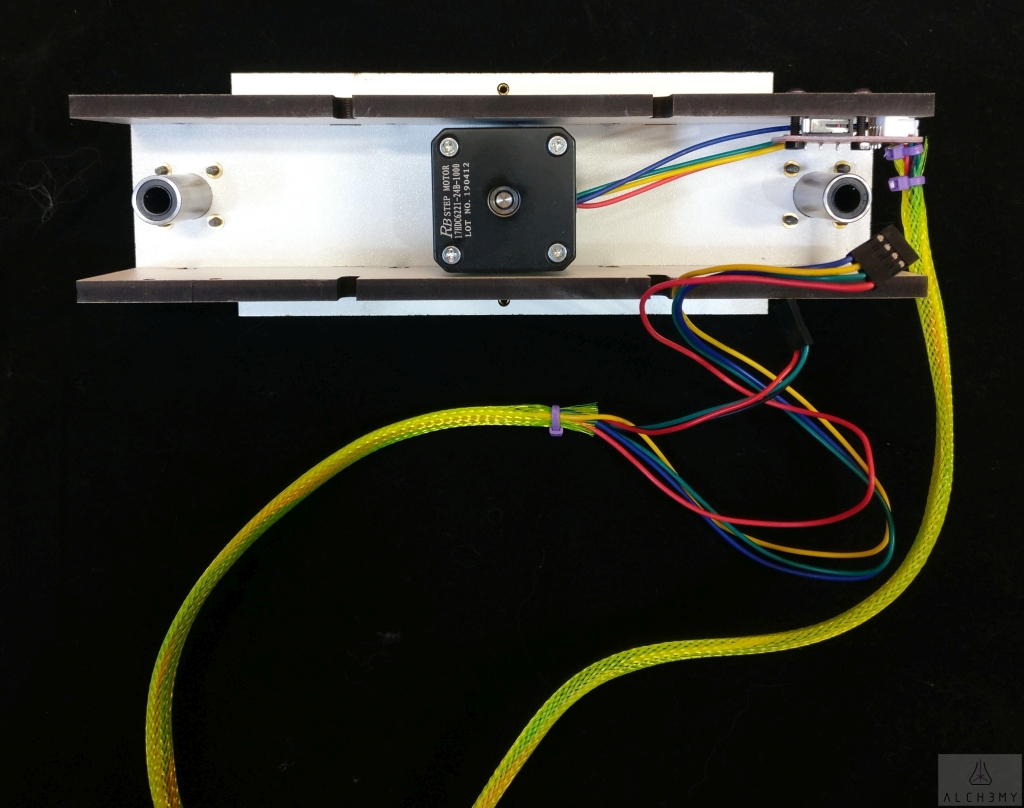
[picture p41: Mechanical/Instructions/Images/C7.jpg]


Figure C7. Wire Management

### Building the Front Drawer
The front drawer is designed to be easily removed. For your safety, there is a endstop switch halts the printer’s operation when either drawer is removed from the printer.

Press in 2 M3 brass press-fit nuts into drawer support. 

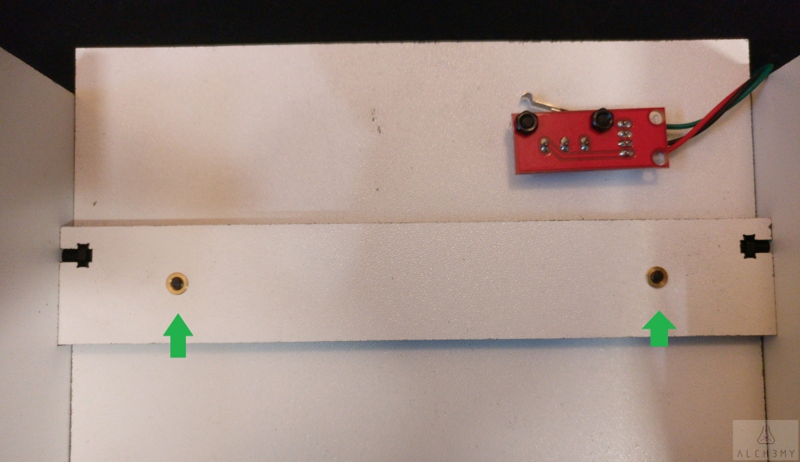
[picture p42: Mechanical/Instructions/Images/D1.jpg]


Figure D1. Drawer Support

Attach drawer support to the front piece with 2 M3x14 screws. Make sure the brass fit nut are on facing out and not sandwiched between the two pieces.

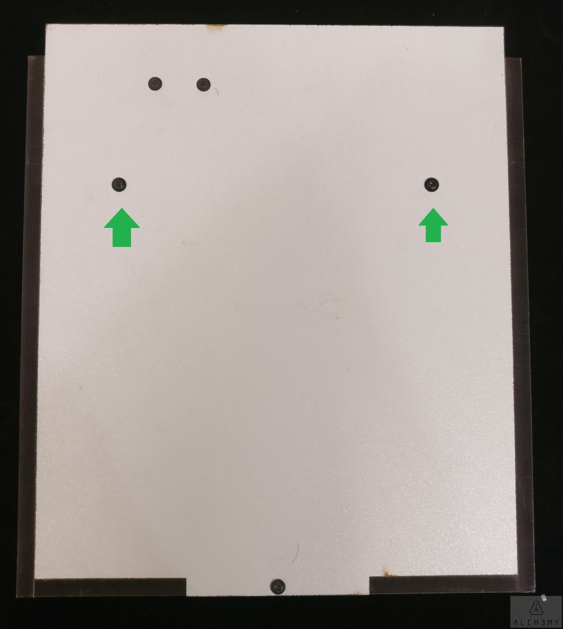
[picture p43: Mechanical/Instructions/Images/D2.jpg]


Figure D2. Install Drawer Support

Attach the drawer bottom to front with 1 M3x14 screw and 1 M3 nut.

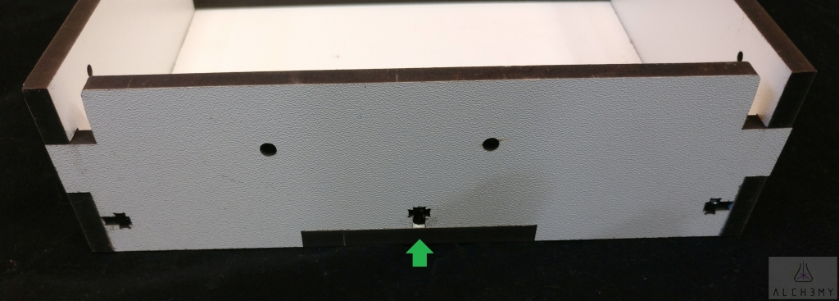
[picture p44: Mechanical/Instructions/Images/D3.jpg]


Figure D3. Drawer Bottom

Attach the sides of the drawers with 2 M3x14 screws and 2 M3 nuts each. A total of 4 M3x14 screws and 4 M3 nuts will be used.

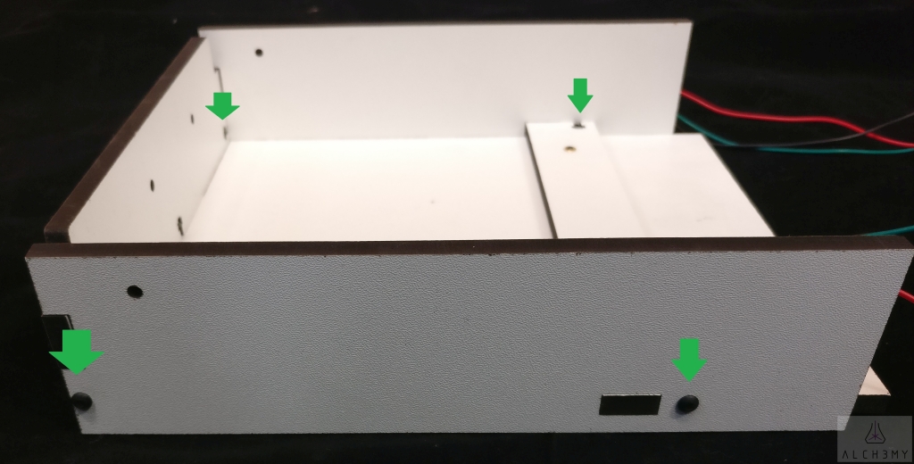
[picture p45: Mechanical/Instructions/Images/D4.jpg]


Figure D4. Drawer Sides

Secure the endstop to drawer front with 2 M3x16 screws. The endstop body and not the PCB should be flush against the wood. Note the end stop switch location.

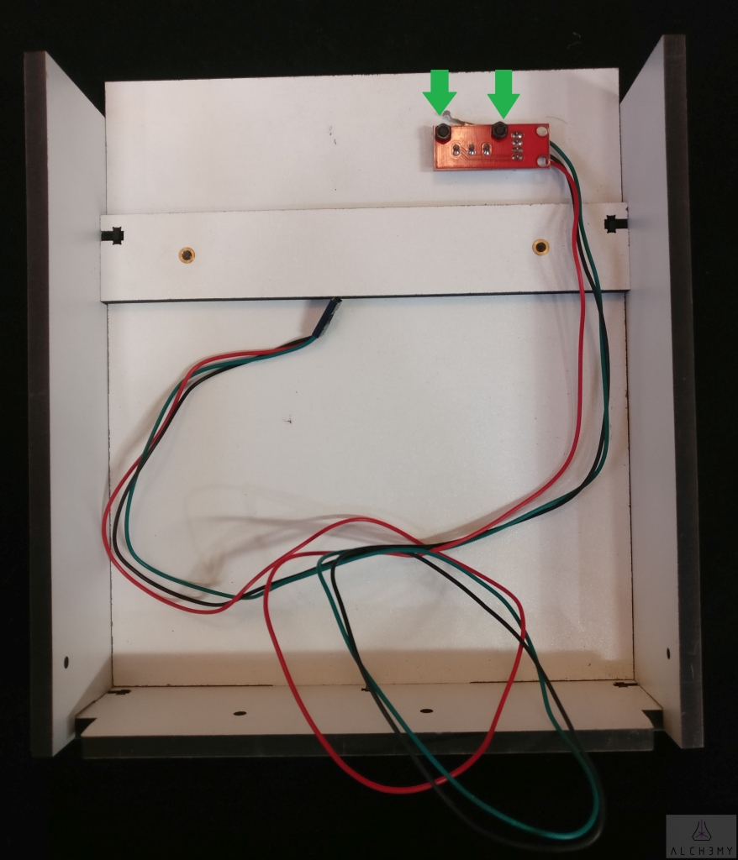
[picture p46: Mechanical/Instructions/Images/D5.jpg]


Figure D5. End Stop

### Building the Back Drawer
The back drawer differs slightly from the front. The back drawer holds all the electronics. The openings for the Arduino USB and power ports.

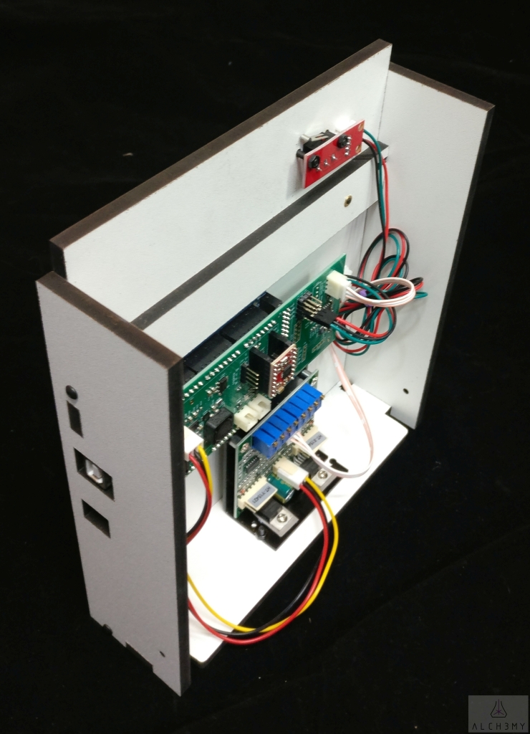
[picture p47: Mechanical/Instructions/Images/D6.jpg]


Figure D6. Back Drawer

Use 1 M3x14 screw and 1 M3 nut to secure galvanometer driver in place.

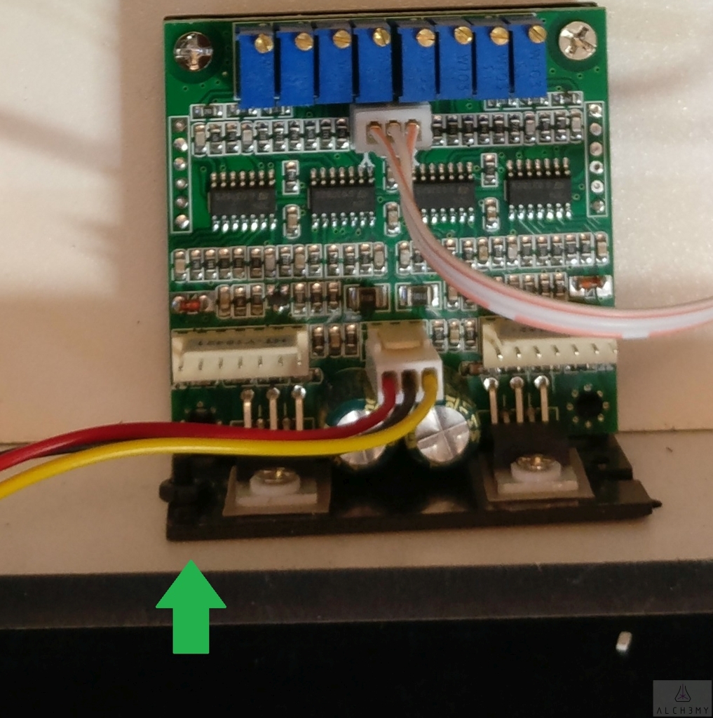
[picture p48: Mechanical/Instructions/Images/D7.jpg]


Figure D7. Galvo Driver

Install the stepper driver board onto Resin Shield. __Line up the EN pins__. Install the Resin Shield onto Arduino Mega and adhere the Arduino Mega to drawer with double sided foam tape. Stacking 2 layers of tape may be necessary depending on height of through hole components. Routing end stop wire, galvo power cable, galvo signal cables. Finally, add 2 adhesive pads for future wire management. A full wiring diagram can be found in a later section.

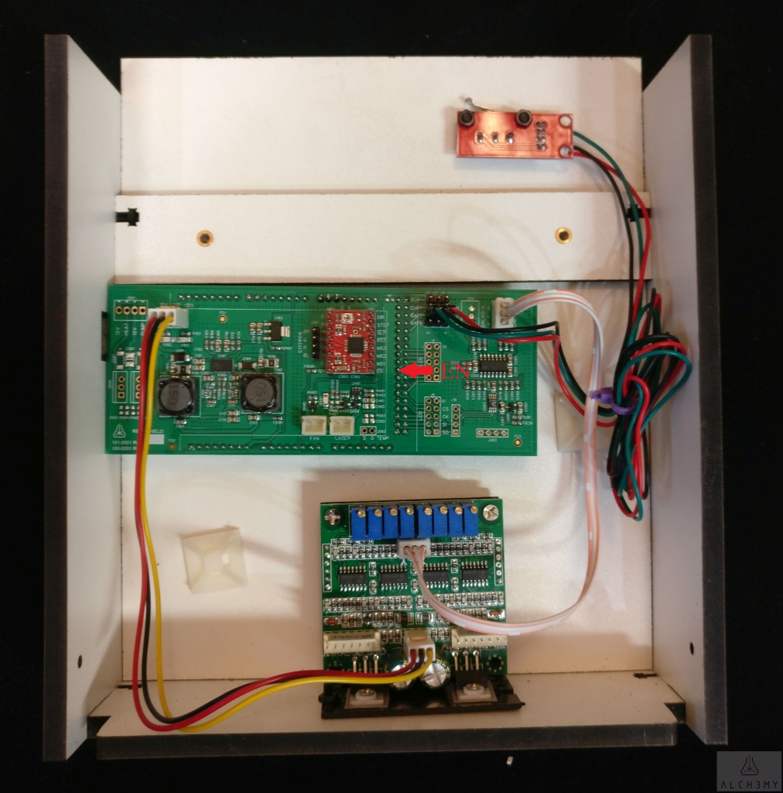
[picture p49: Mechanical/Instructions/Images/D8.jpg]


Figure D8. Mounted Electronics

### Building the Frame
The frame holds everything together. Although most parts in this printer kit are built with symmetry in mind, some of the pieces of the frame are direction dependent. 

There are two slots on the carrier, they are for the end stop switches on the drawers from the previous step. In the top view, the slots should be __front-left__ and __rear-right__. 

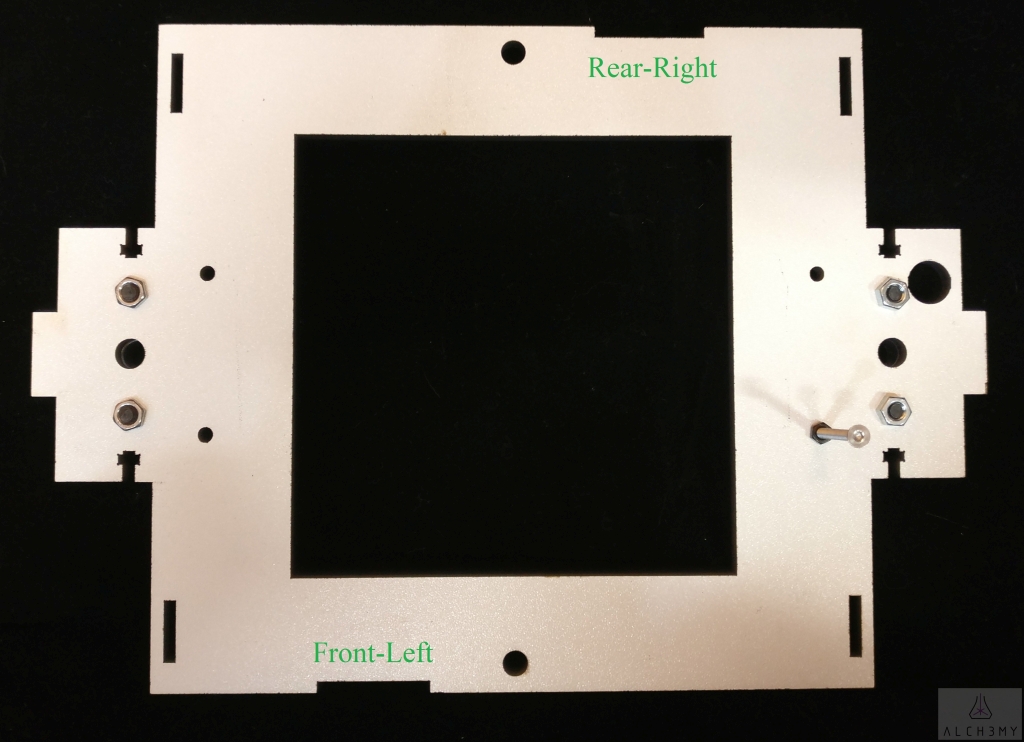
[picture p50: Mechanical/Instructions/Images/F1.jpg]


Figure F1. Top View

Attach the 2 SHF8 (8mm linear rail holders) on to the carrier using 4 M5x20 screws and 4 M5 nuts. The flat on the SHF8 should point inside, it enables easier access to the clamping screws.



Figure F2. SHF8 Installed

Attach the Z end stop's adjustment M3x50 screw by pressing a M3 brass press-fit nut from the bottom in the __front-right__ hole, thread a M3 nut onto the adjustment screw first, and then thread the screw onto the nut. The nut is used to secure the adjustment screw. 



Figure F3. Z End-Stop Adjustment Installed

Install the two 8mm linear rails onto the SHF8 and install the crane into the rails. 



Figure F4. Carrier and Linear Rails Installed

Slide the frame back piece onto the carrier, use it as a guide to set the linear rail's height. Note there is a raised laser holder feature on the __left__ side of the frame back piece. Tighten the SHF8 locking screws, this can be adjusted later to make everything flush.



Figure F5. Carrier and Linear Rails Installed

Slide the frame front piece onto the carrier, make sure to orient the laser holder feature on the __left__ side. Now install 4 M3x14 screws and 4 M3 nuts to secure both frame pieces onto the carrier. Keep these screws slightly loose for now.



Figure F6. Frame Front and Back secured

Place the 8mm to 5mm flex coupler onto the 8mm ACME screw, adjust until the 8mm ACME does not cover any of the spring portion of the flex coupler (approximately 8mm of insertion depth). Tighten the 2 set screws on the flex coupler to secure. Install the assembly onto the frame top piece with 4 M3x14 and 4 M3 nuts.



Figure F7. Frame Top and ACME Assembly

Place frame top onto the main frame assembly. Install frame sides as well. Tighten the previously loose 4 frame screws.



Figure F8. Frame Held Together

Install 10 M3x14 screws and 10 M3 nuts to secure frame top. Adjust 8mm rails if necessary to make them flush at the top.



Figure F9. Frame Top

Install 8 M3x14 screws and 8 M3 nuts to secure the frame sides.



Figure F10. Frame Sides

Install 10 M3x14 screws and 10 M3 nuts to secrure the frame bottom. Note the frame bottom has a slot, it goes towards the __back__.



Figure F11. Frame Bottom

Secure the NEMA17 stepper motor's shaft onto the M5 to M8 flex coupler, use about 8mm of overlap. Make sure to put one set screw on the D portion of the shaft. 



Figure F12. Flex Coupler

Install both frame feet with 4 M3x14 and 4 M3 nuts. Also press in 4 M3 brass press-fit nuts onto the feet, the flange should be on the __inside__.



Figure 13. Feet

Install laser onto the laser holder piece with 4 M3x14 screws. Note the laser is pointing at the wider side of this piece.



Figure 14. Laser Holder

Press 2 M3 brass press fit nuts onto the galvo holder, then install the galvo using 3 M4x10 screws. Do your best to keep the galvanometer parallel to this piece. This sets the initial X and Y offset of the printer, we will calibrate this later. __Be careful with the mirrors.__



Figure 15. Galvanometers

Install the laser holder onto the frame using 2 M3x14 screws and 2 M3 nuts, then the galvo onto the frame using 2 M3x14 screws. Tidy up the wires using the provided wiring channels.



Figure 16. Galvanometers and Laser

Install the orange acrylic accent pieces onto the crane using 2x M3x10.



Figure 17. Accent Piece

Install 2 M5 standoffs and 2 M5 nuts on the carrier. Next use clear tape to hold down the removable clear print plate onto the carrier. Note the print plate is not square, please make sure the wider side goes over the left and right edge of the hole in the carrier. This print plate also gives additional tension to the FEP film (future steps). 



Figure 18. Standoffs and print plate

### The Build Platform
Sand the bottom of the build platform with rough sandpaper for better print adhesion. All the holes on the sides are for drainage since the build platform is partially submerged in resin at the beginning of the print. Use 4 M5x20 screws to install the build platform on the crane. For future removal, simply loosen the 4 screws and pull the print and build platform away from the crane.



Figure P1. Build Platform

### Reusable Resin Reservoir
This step is crucial for the quality of print, make sure to proceed slowly and ensure a water-tight finish in the end.

1. Place a ring of double sided adhesive (provided) as high as possible along the vertical reservoir exterior wall.
2. Remove FEP film from backing. FEP is clear and slightly stretchy, the backing is made of PTFE and is not stretchy.
3. Place the aluminum resin reservoir on top of the FEP film and fold the FEP around the resevoir. Make sure the FEP film is tightly stretched and well adhered to the double sided tape.
4. Cover the FEP's vertical surface with single sided tape (provided).



Figure R1. Completed Reservoir

Install the reservoir onto the frame using 2 M5x20 screws. The slightly thick print plate provides additional tension to the FEP film, make sure there are no bubbles or gaps between the FEP film and the print plate.



Figure R2. Installed Reservoir

The reservoir can be removed easily for cleaning. If worn out, the FEP can be replaced by repeating the above steps.

### Electrical Hookup Diagram
Connect all the electrical cables. Pay special attention to the following:
1. Switches: Signal (S) is green, Ground (-) is black, 5V (+) is red. Z end stop switch connects to the ZMIN port. The other door switches connect to the SAFE ports.
2. NEMA17 stepper motor: they come with 4 wires of various colors depending on manufacturer, if you later find the Z direction is reversed, just flip this connection backwards.
3. The laser module: the fan and laser power use identical connectors. The fan cable is longer and thinner.
4. The galvos: x-axis is the galvo installed vertically, it's responsible for the laser going left and right. Y-axis is the galvo installed horizontally, it's responsible for the laser going back and forth.

Figure E1

Figure E1. Electrical Hookup Diagram

Use zip ties, anchors, and tape to neatly arrange the wires.

### Finishing Touches

Install the drawers onto the frame and secure using 4 M3x14 screws.



Figure 19. Installed Drawers

Install the side accent windows and secure with clear tape.



Figure 20. Windows

Slot in the front and back doors. Make sure it engages the safety switches with a satisfying click. With proper installation, if a user removes either door or drawers mid print, the print will halt and the laser will be immediately extinguished.

Figure F21

Figure 21. Fully Built

### Published by Alch3my LLC 

### CERN OHL v1.2 license whenever applicable.

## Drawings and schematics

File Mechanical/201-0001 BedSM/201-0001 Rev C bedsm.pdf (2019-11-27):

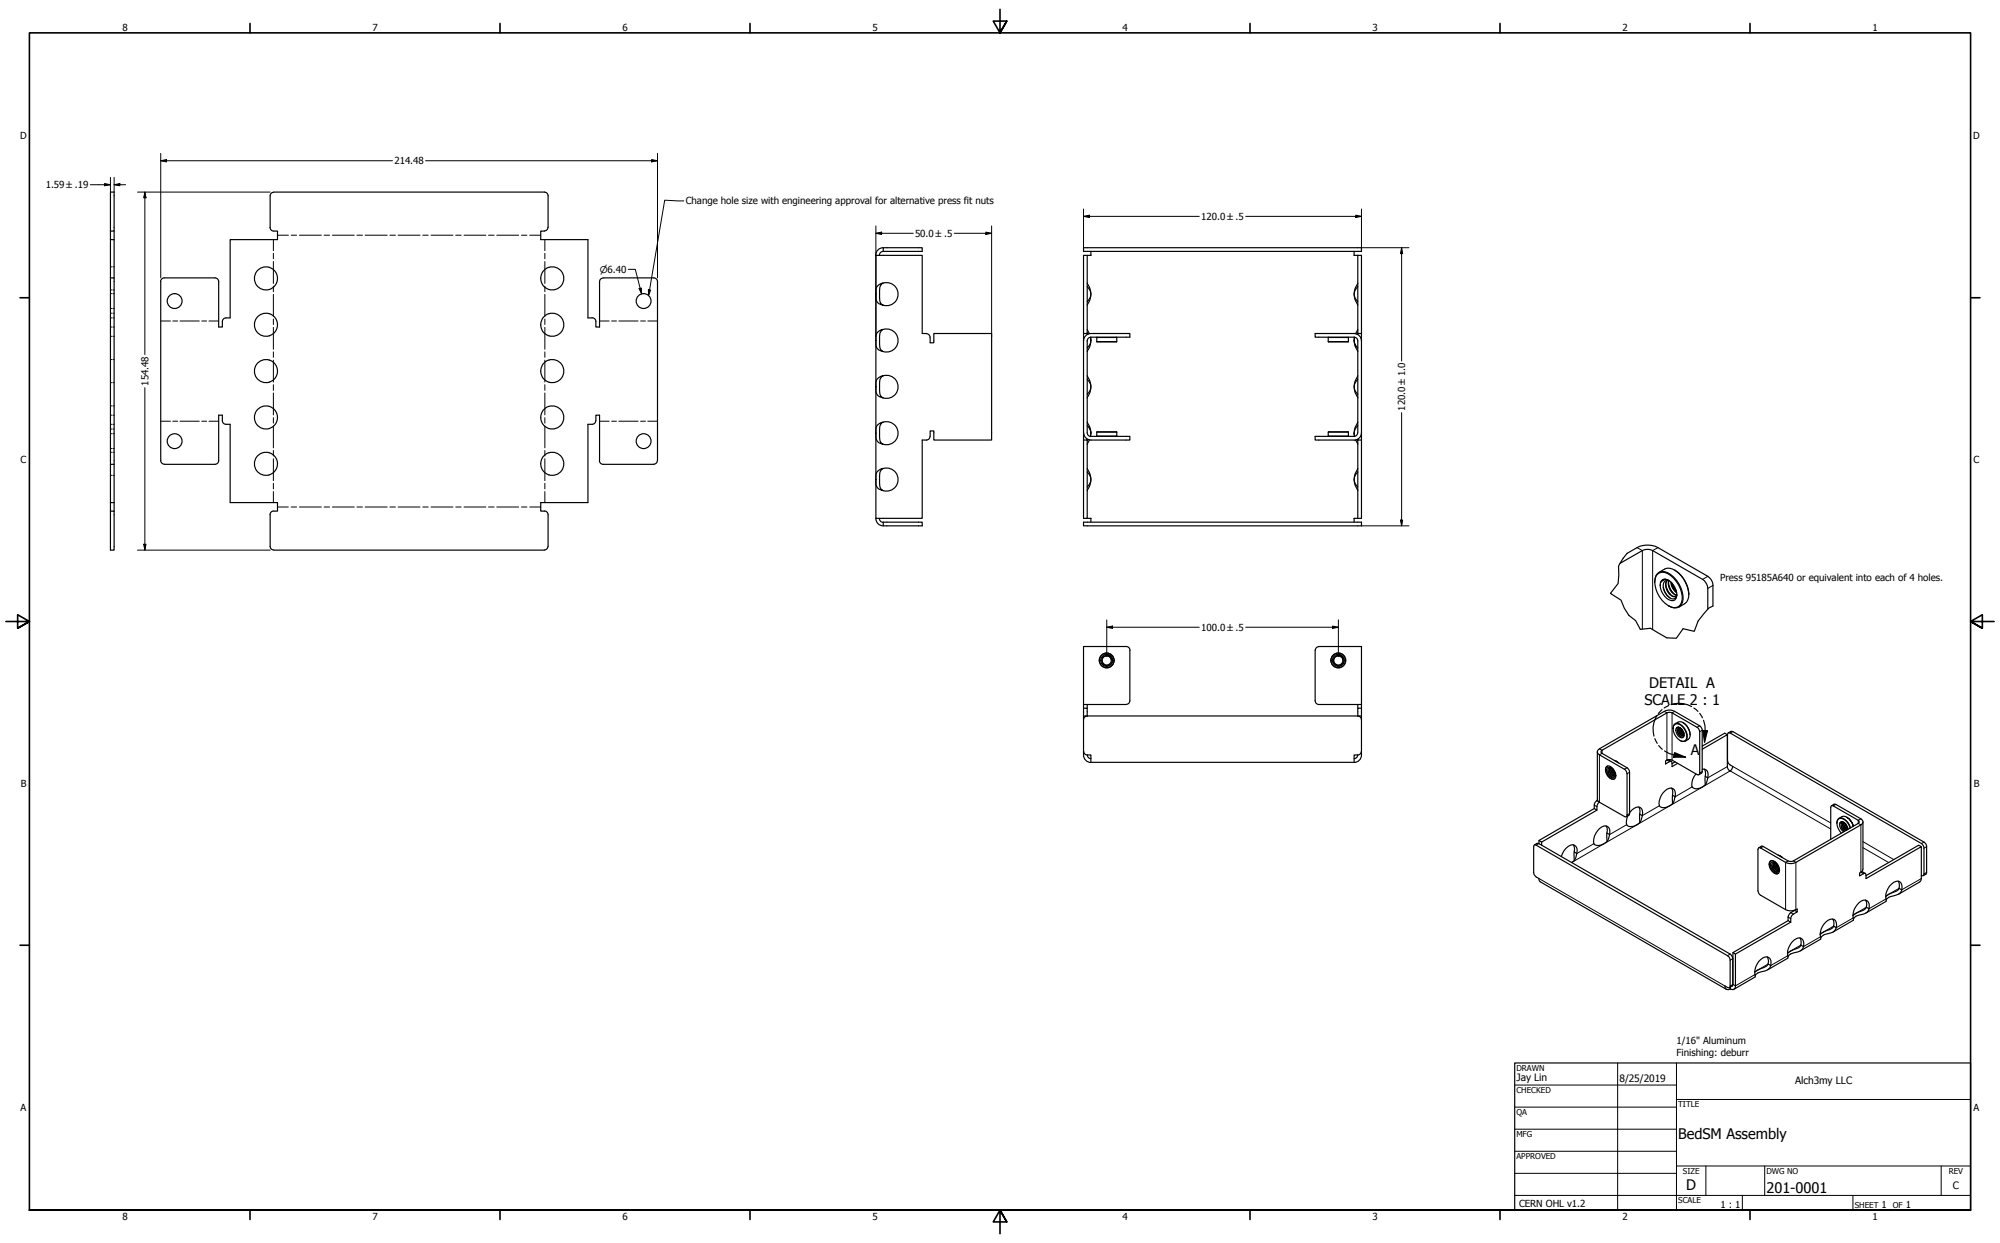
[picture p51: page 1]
DETAIL A SCALE 2 : 1; BedSM Assembly; 1/16" Aluminum Finishing: deburr

Change hole size with engineering approval for alternative press fit nuts

Press 95185A640 or equivalent into each of 4 holes.

DRAWN Jay Lin | 8/25/2019 | Alch3my LLC

CHECKED

MFG

APPROVED

SIZE D | DWG NO 201-0001 | REV C

CERN OHL v1.2 | SCALE 1 : 1 | | SHEET 1 OF 1

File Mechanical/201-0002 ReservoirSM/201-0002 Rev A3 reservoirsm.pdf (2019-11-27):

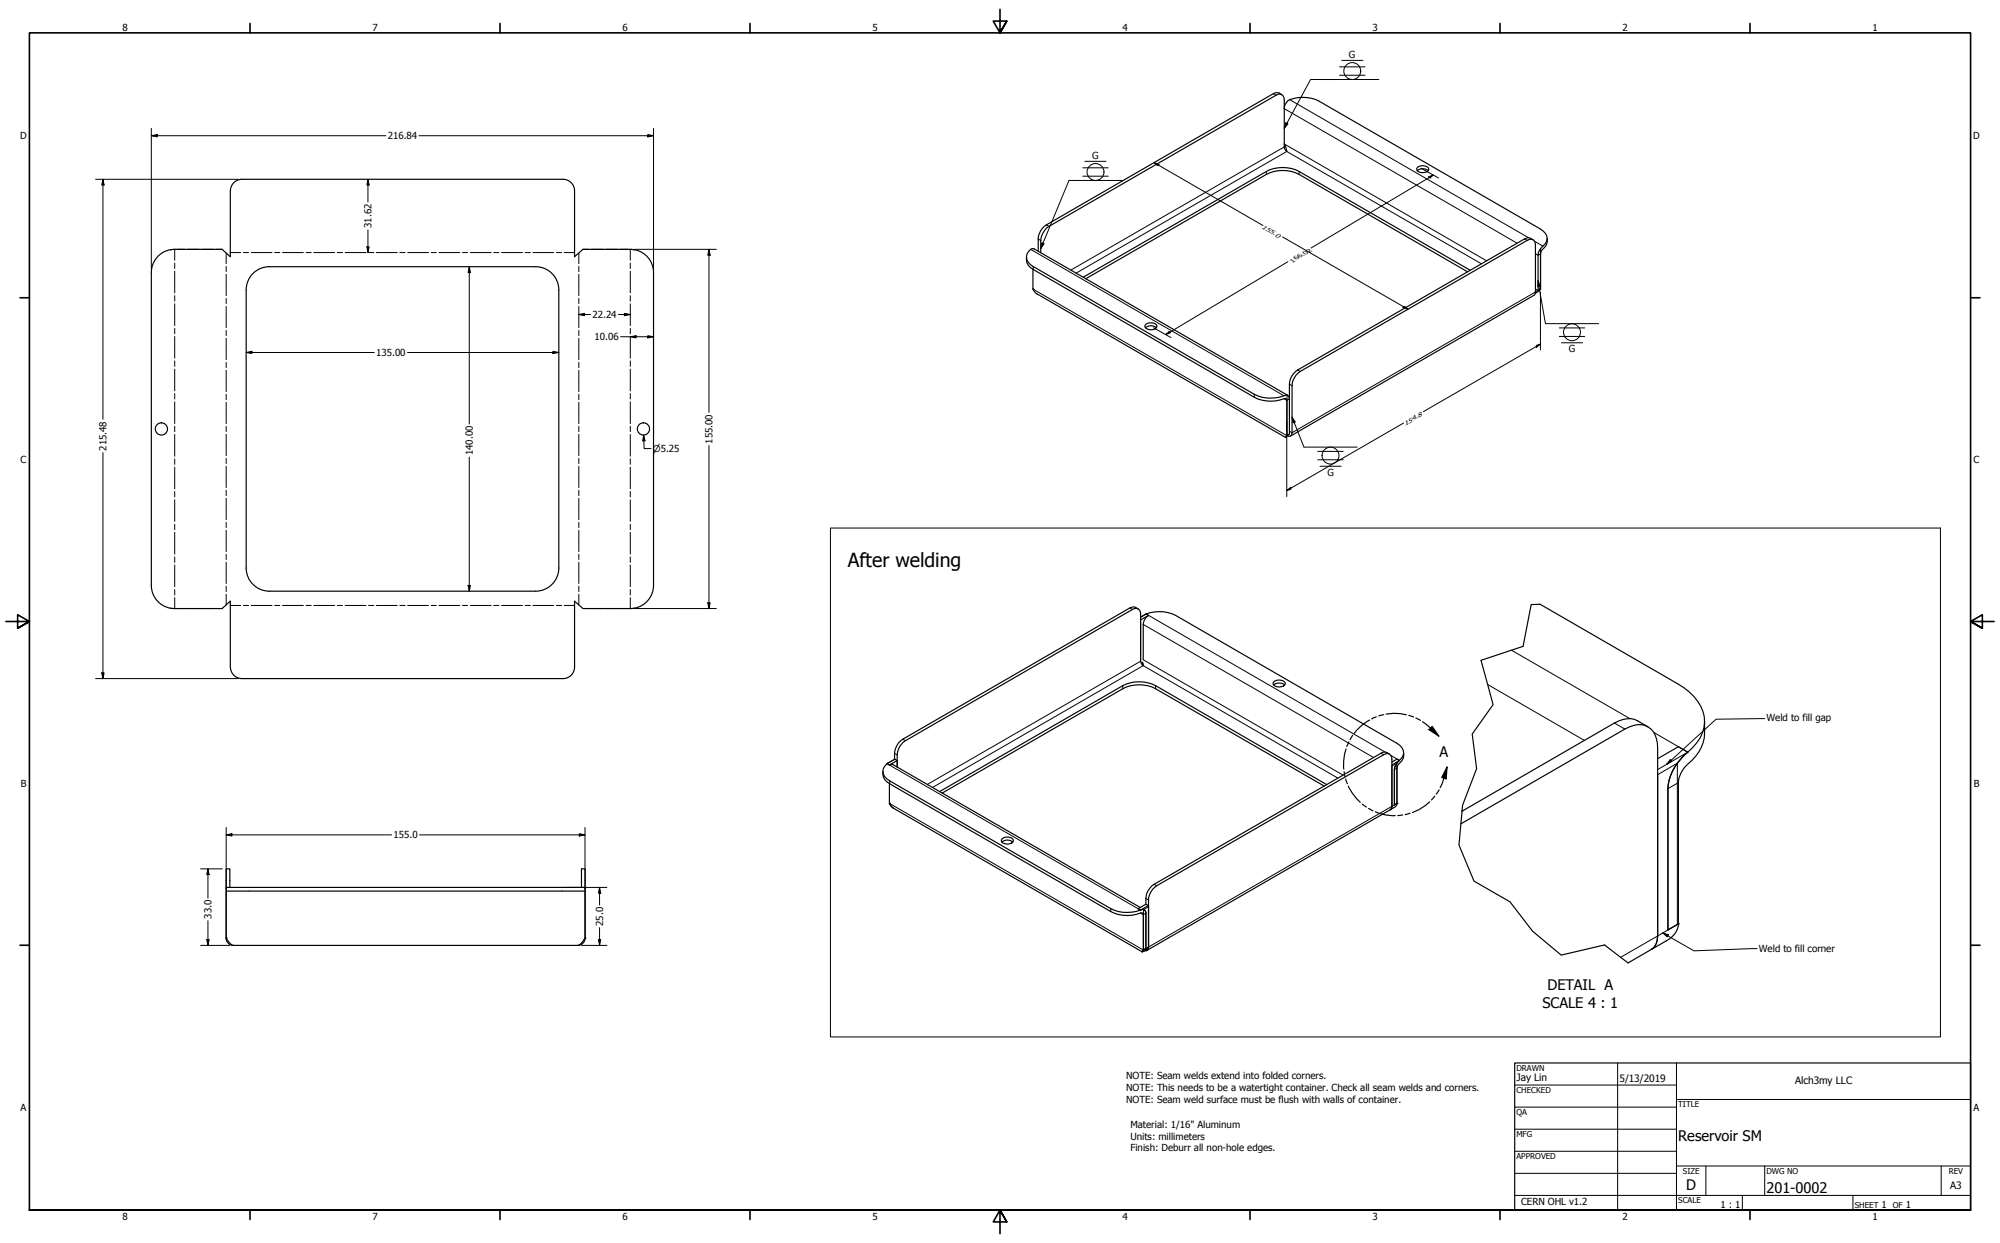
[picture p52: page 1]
DETAIL A SCALE 4 : 1; Reservoir SM; After welding

Weld to fill gap

Weld to fill corner

DRAWN Jay Lin | 5/13/2019 | Alch3my LLC

NOTE: Seam welds extend into folded corners.
NOTE: This needs to be a watertight container. Check all seam welds and corners.
NOTE: Seam weld surface must be flush with walls of container.

CHECKED

Material: 1/16" Aluminum
Units: millimeters
Finish: Deburr all non-hole edges.

MFG

APPROVED

SIZE D | DWG NO 201-0002 | REV A3

CERN OHL v1.2 | SCALE 1 : 1 | | SHEET 1 OF 1

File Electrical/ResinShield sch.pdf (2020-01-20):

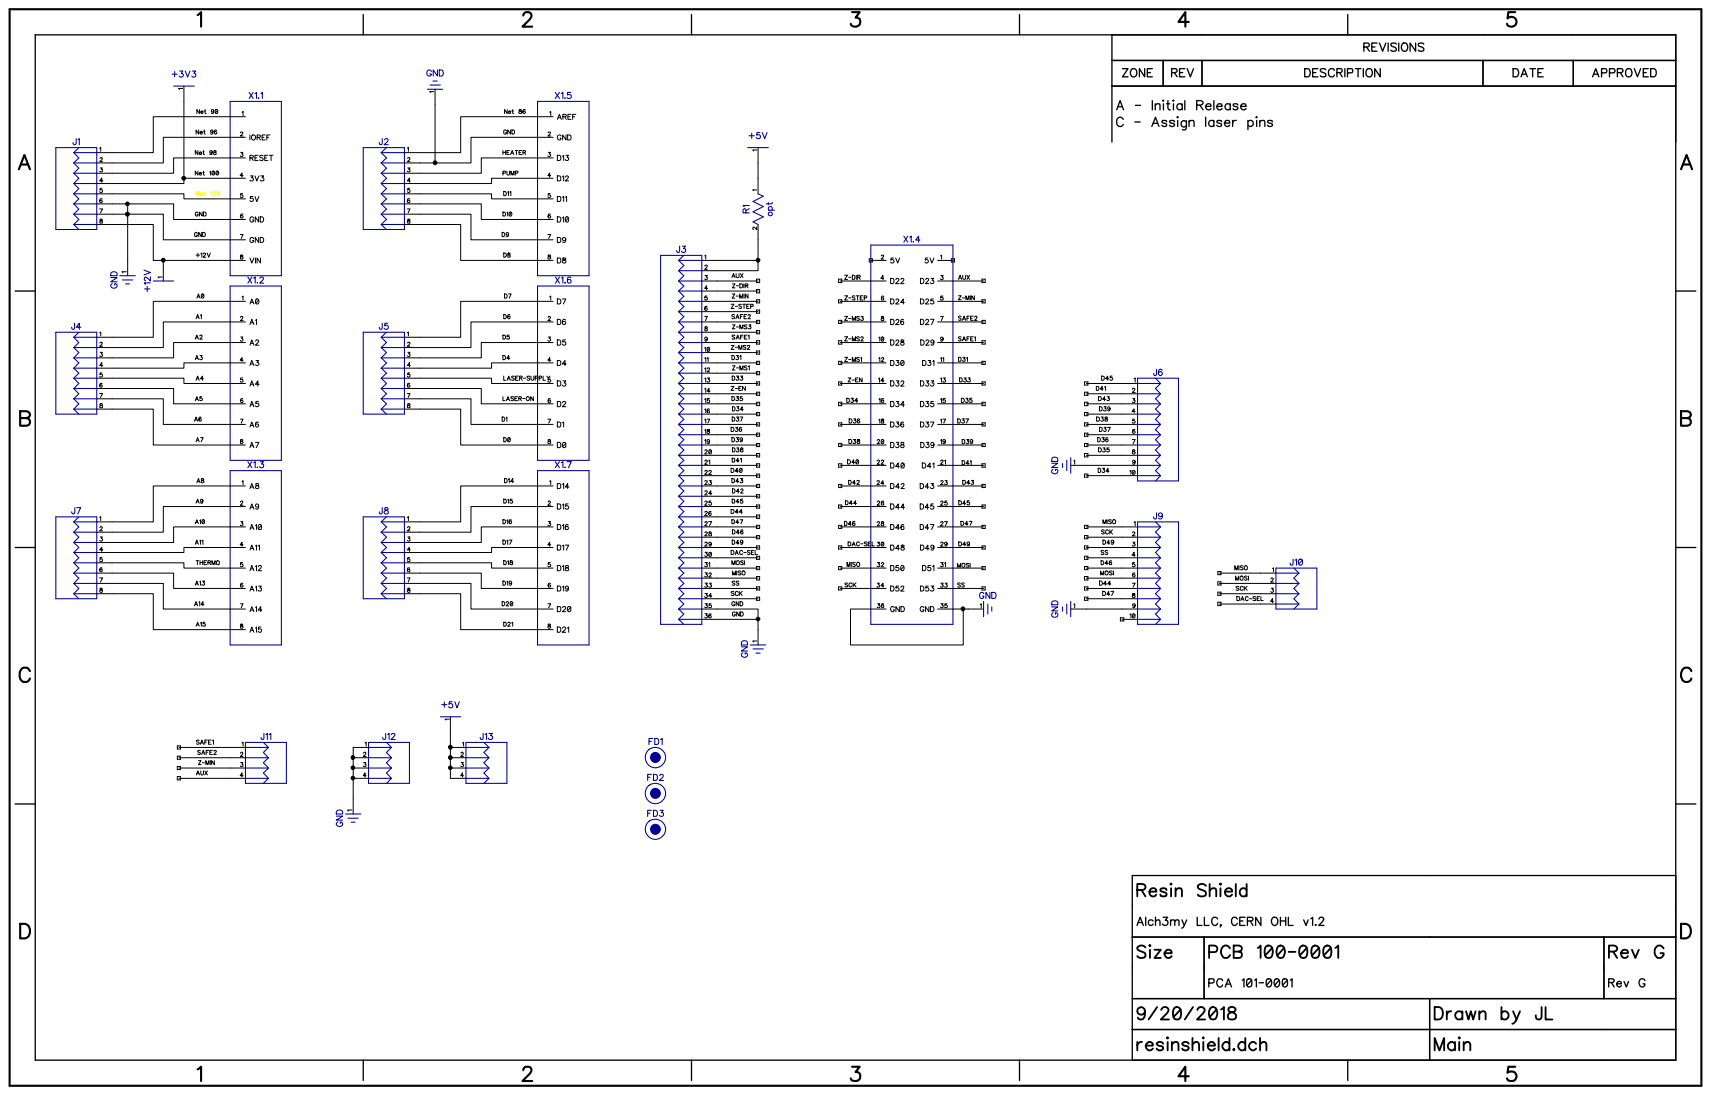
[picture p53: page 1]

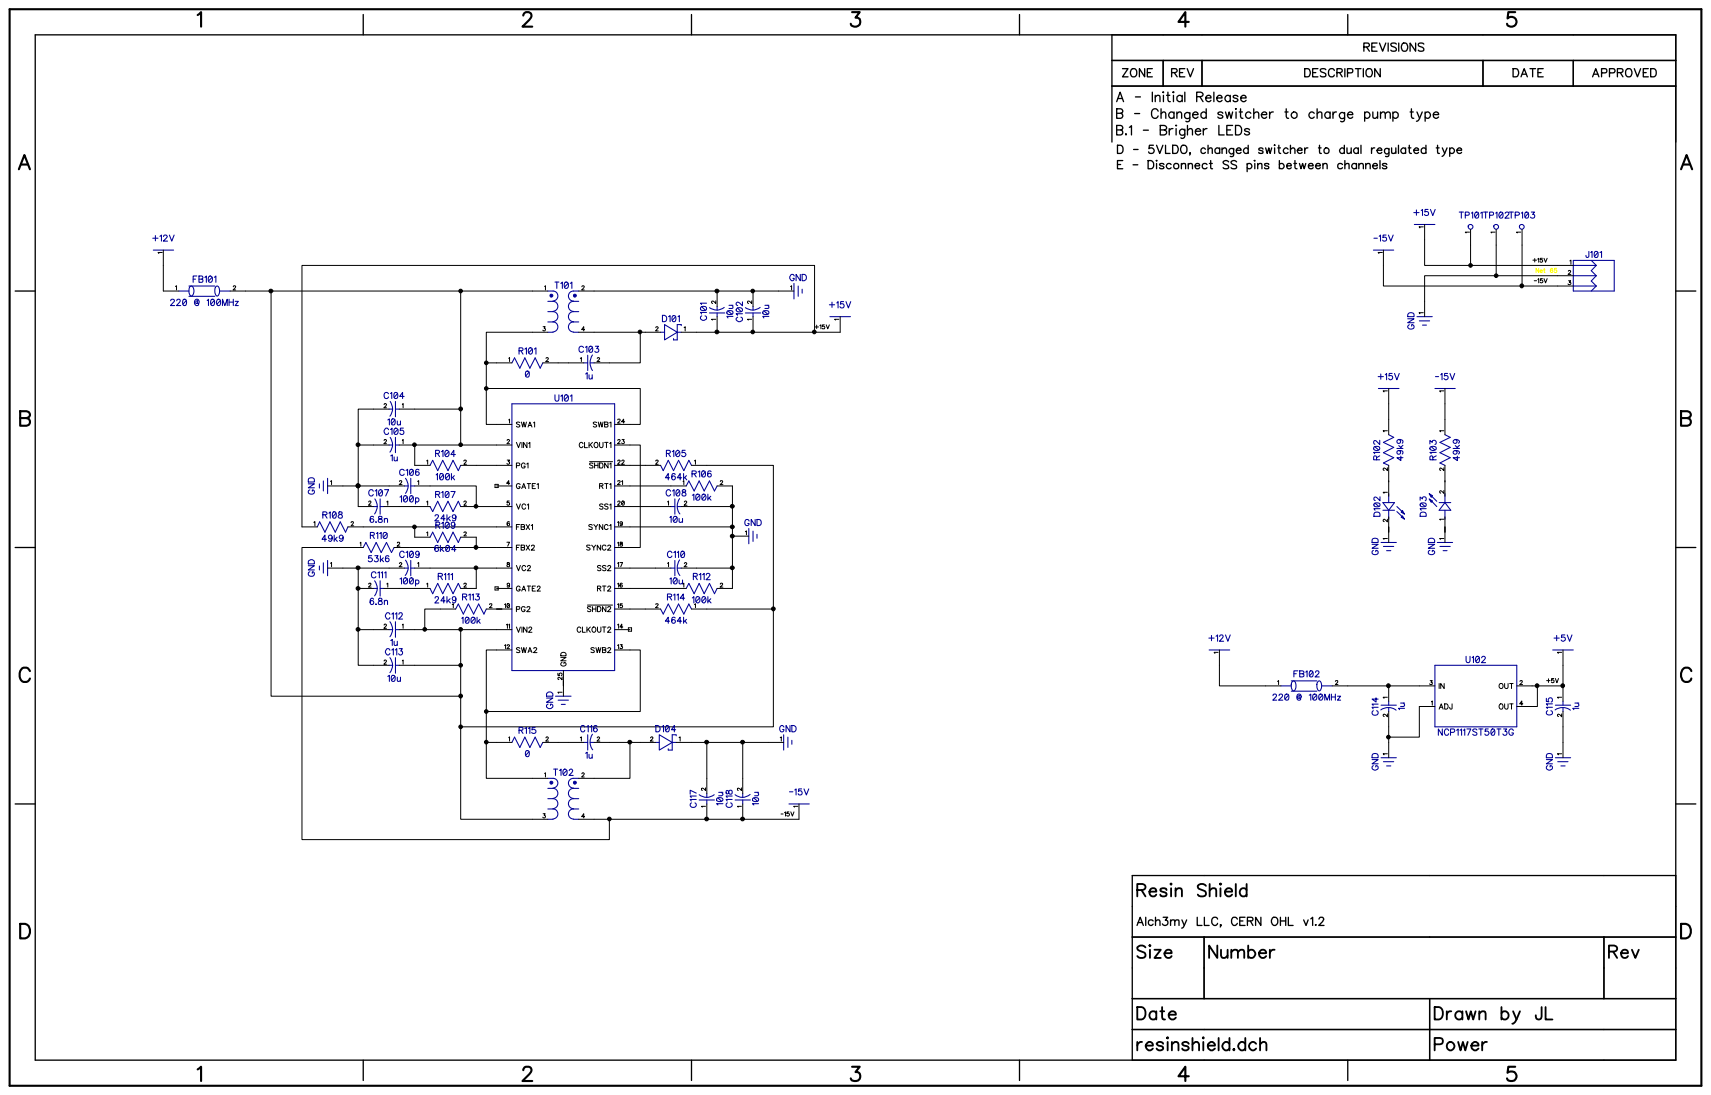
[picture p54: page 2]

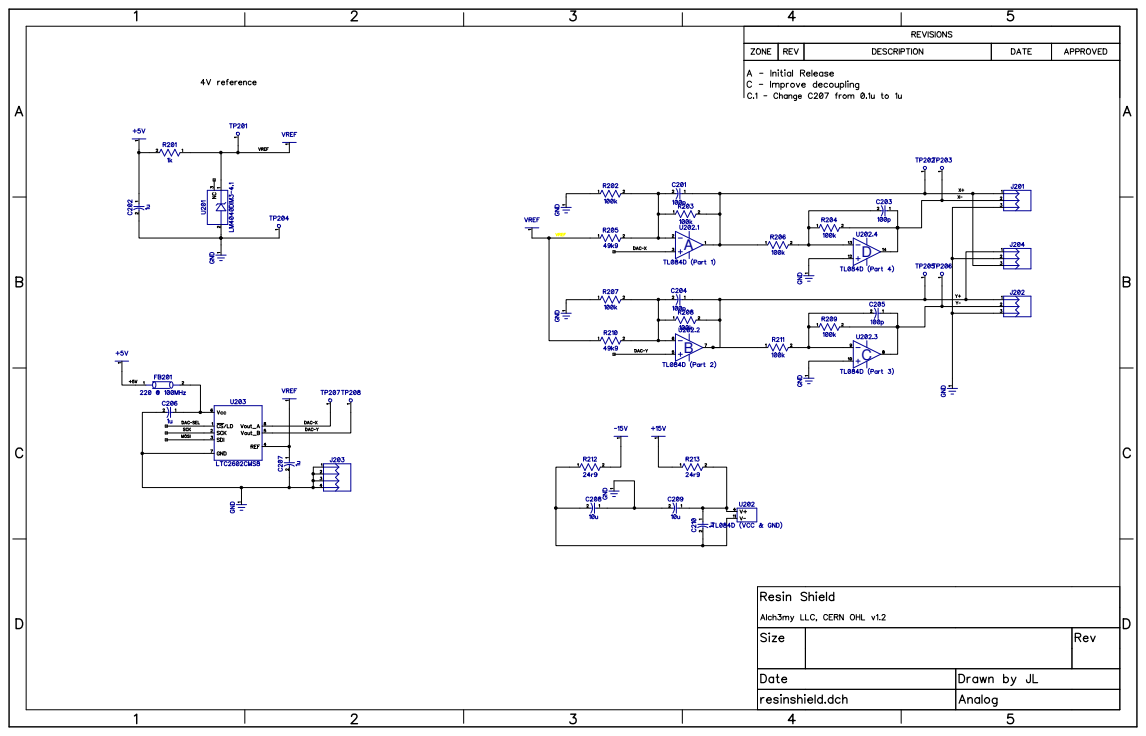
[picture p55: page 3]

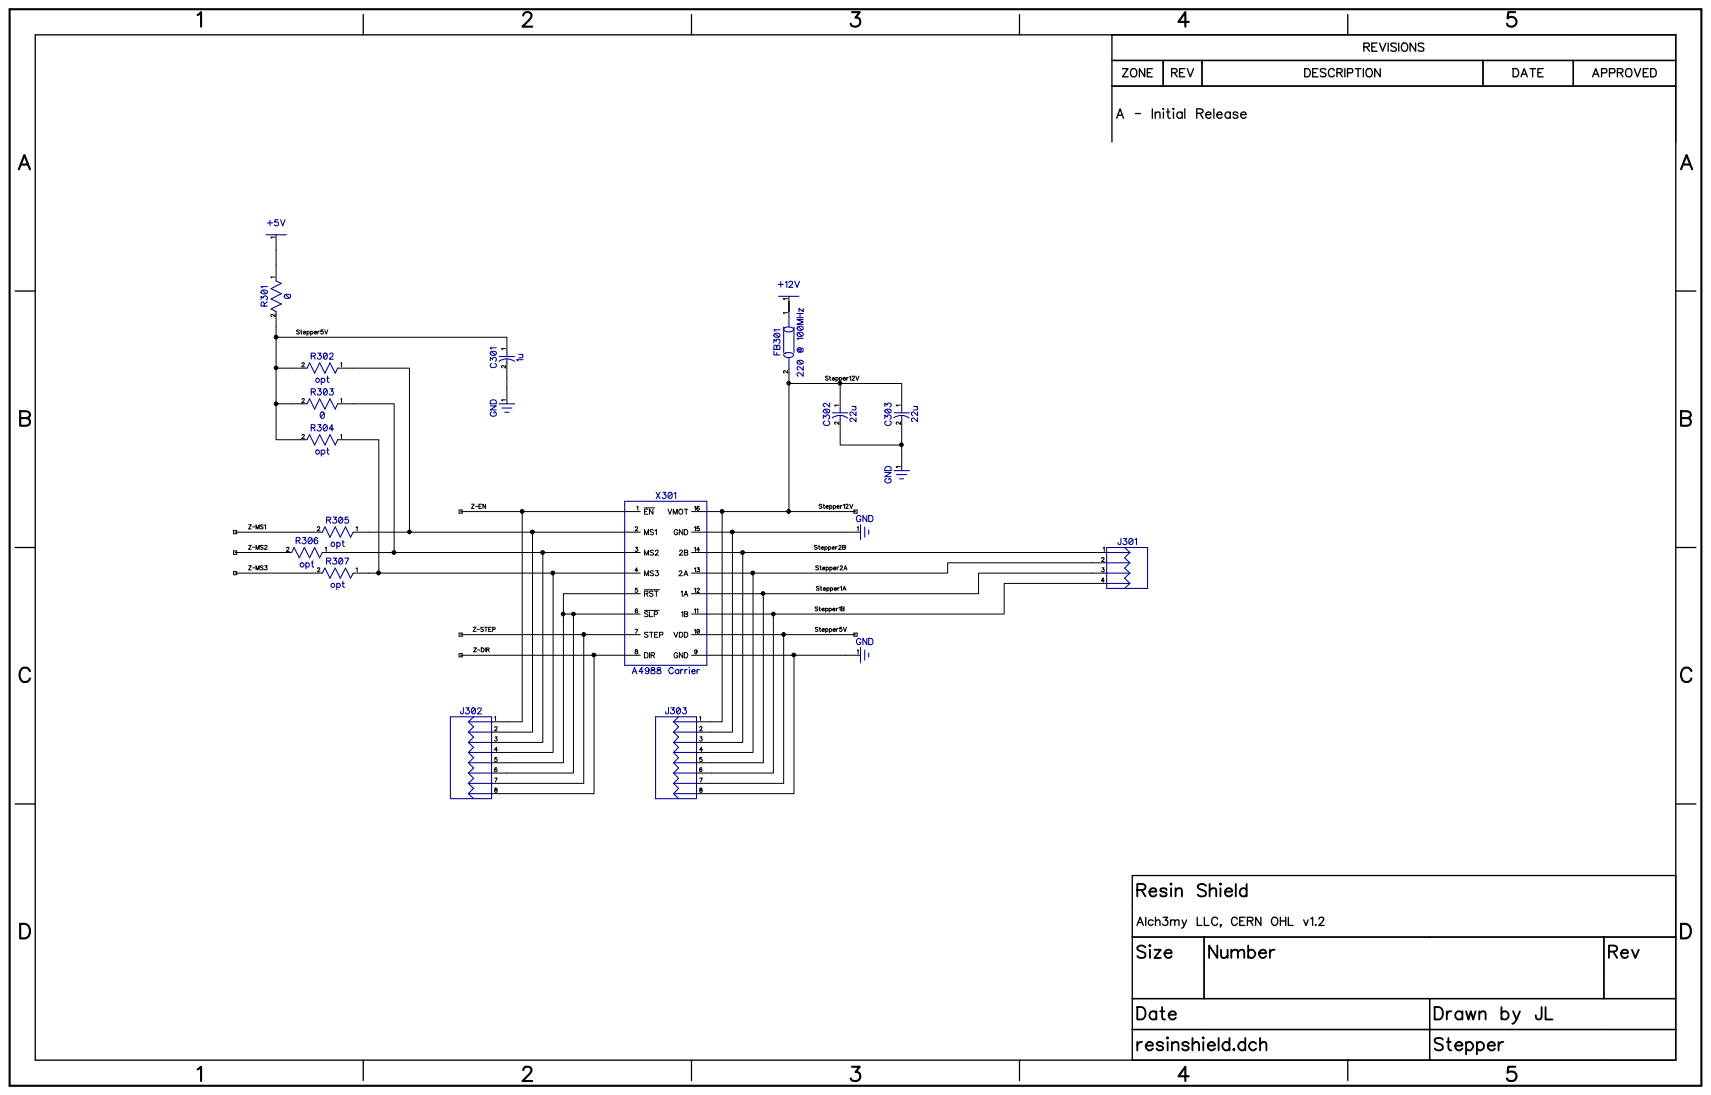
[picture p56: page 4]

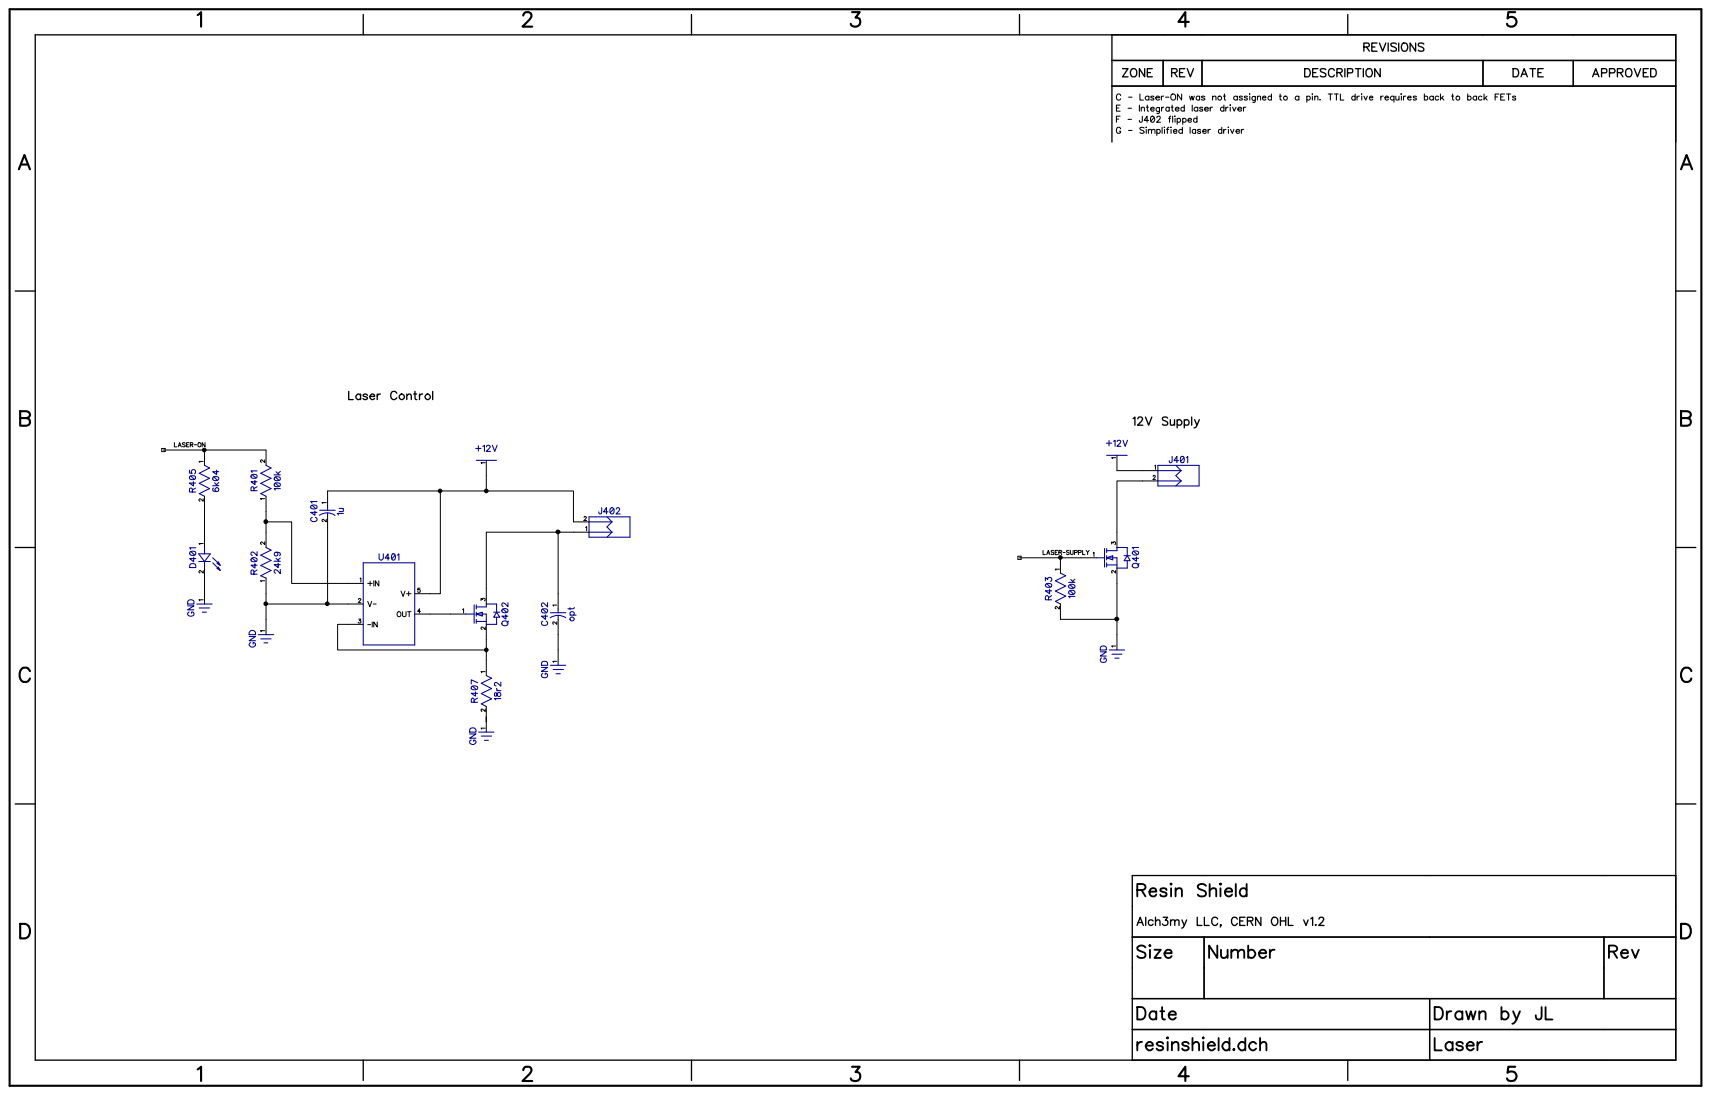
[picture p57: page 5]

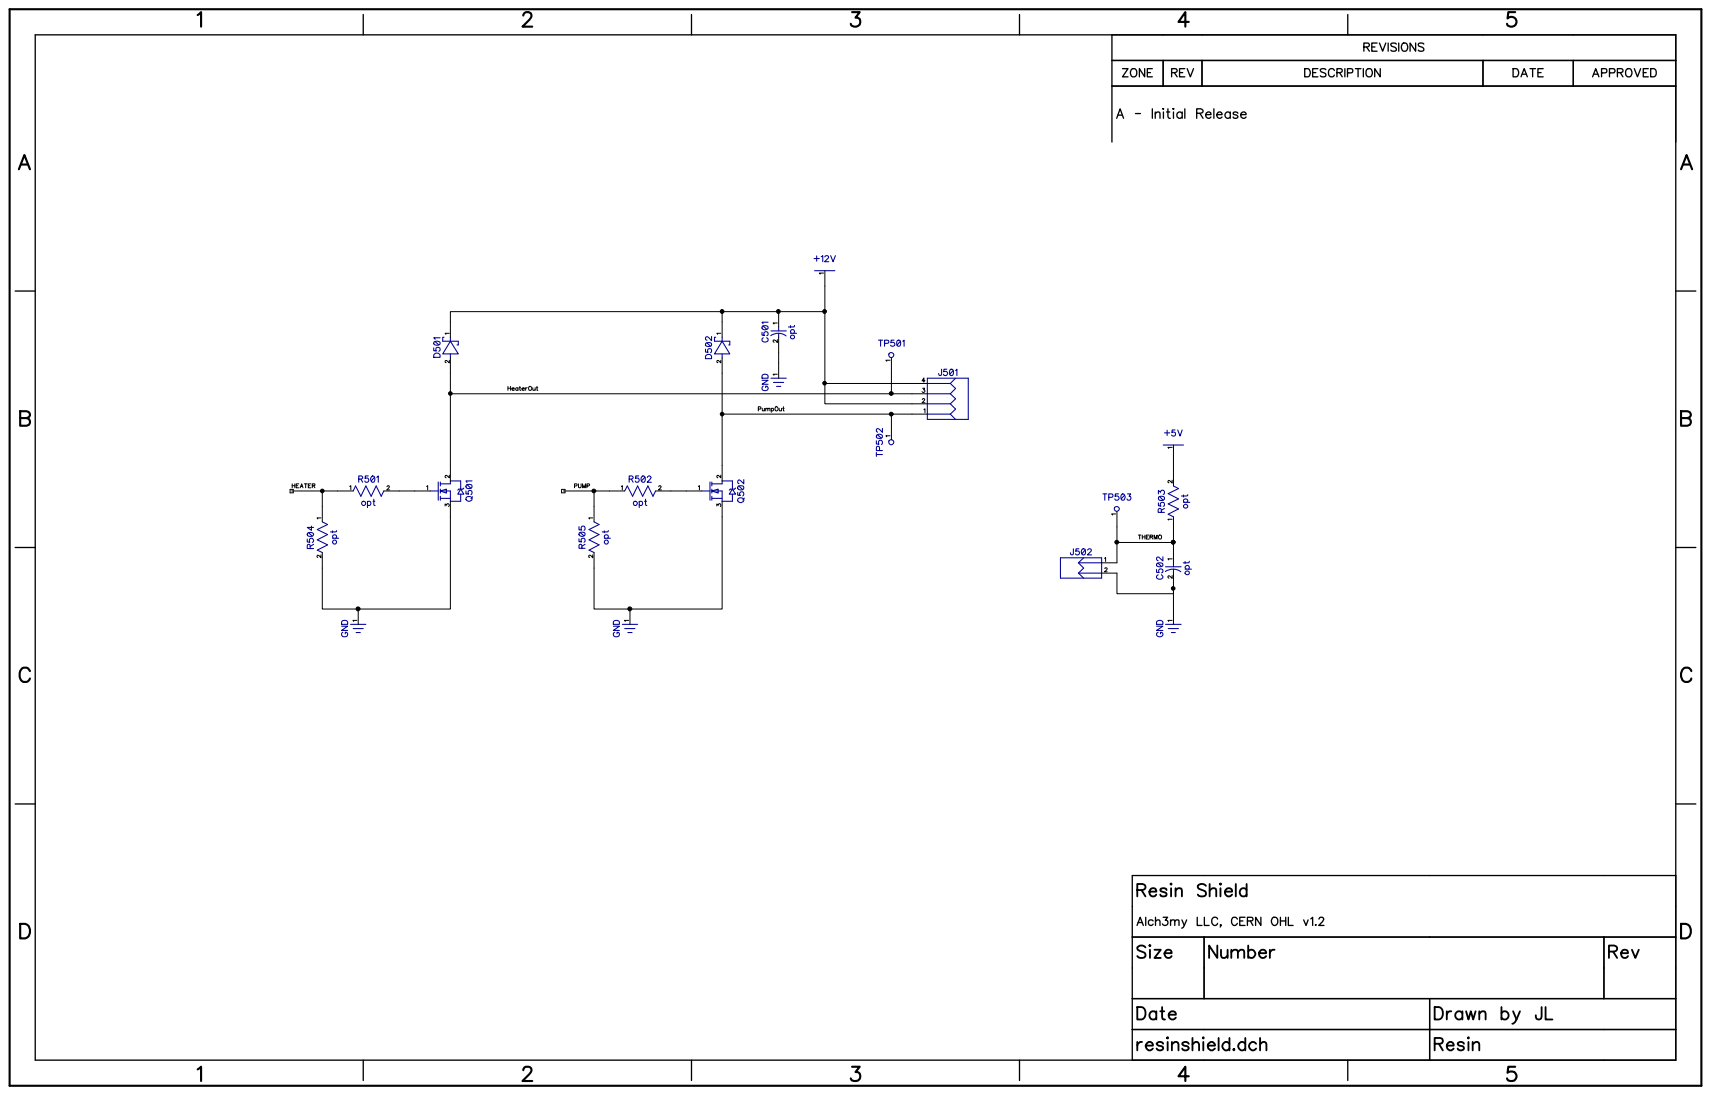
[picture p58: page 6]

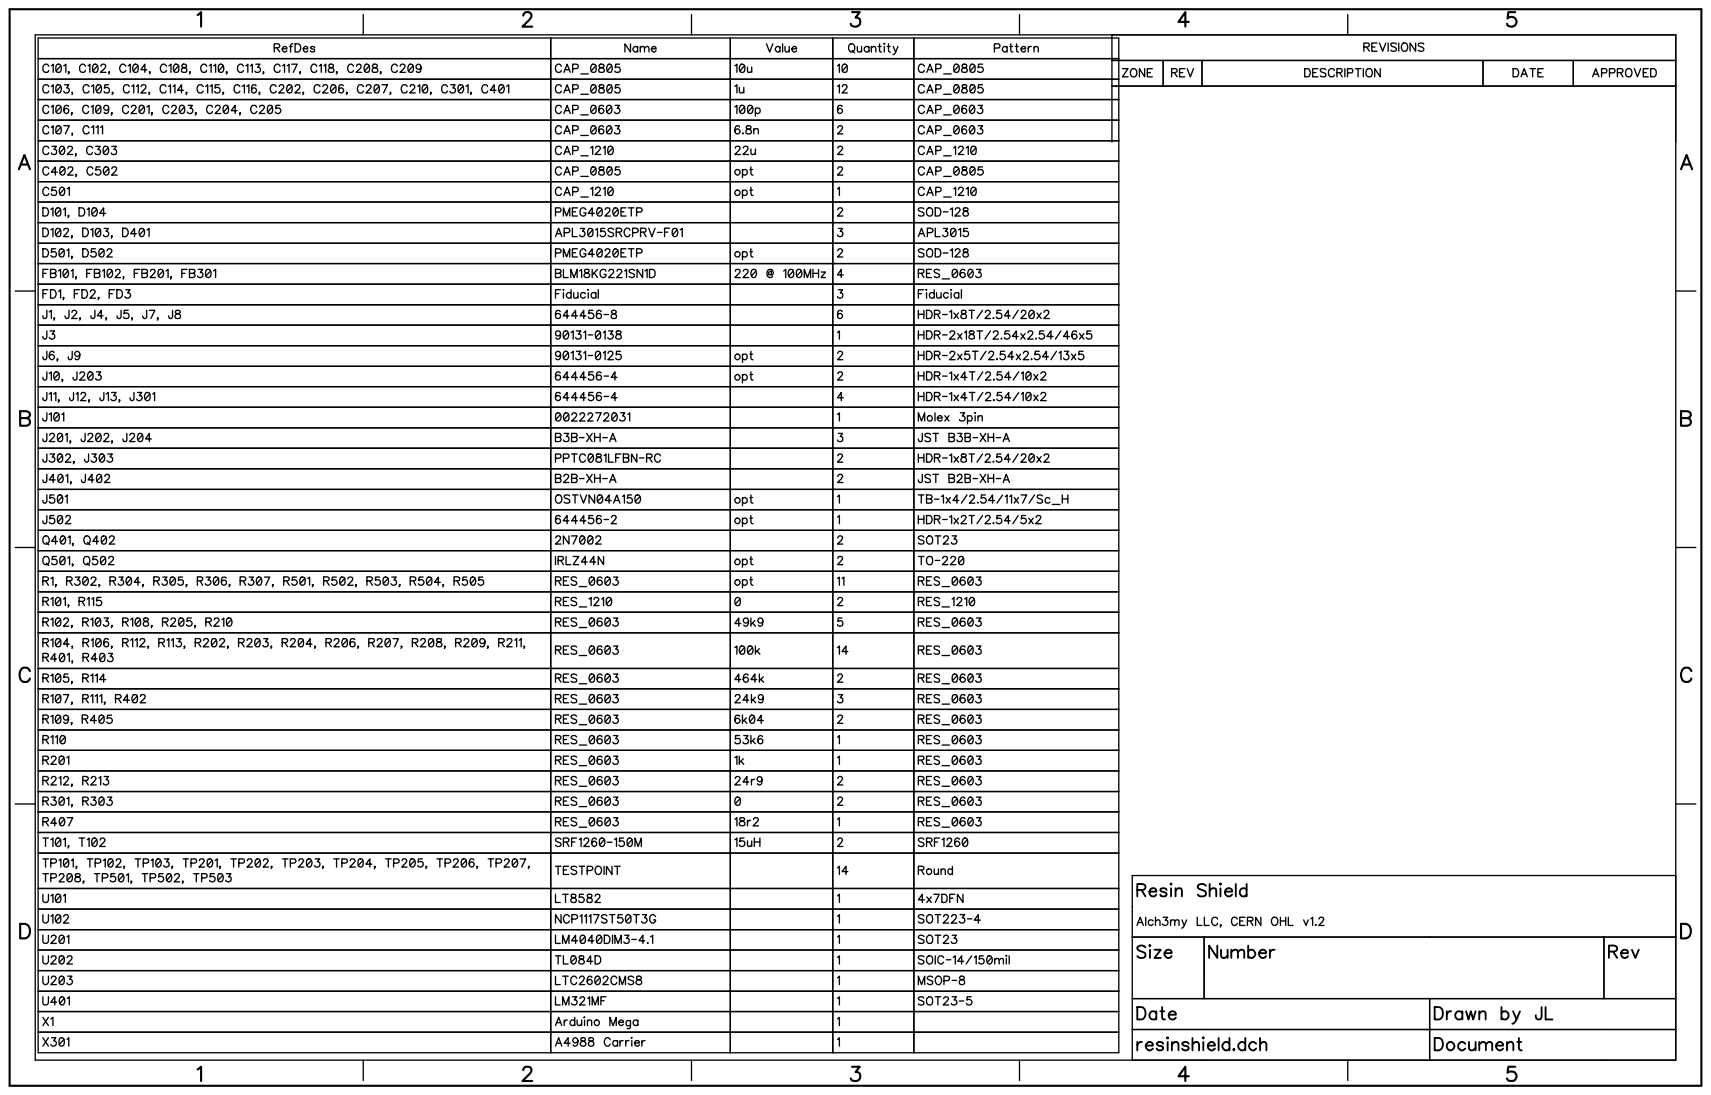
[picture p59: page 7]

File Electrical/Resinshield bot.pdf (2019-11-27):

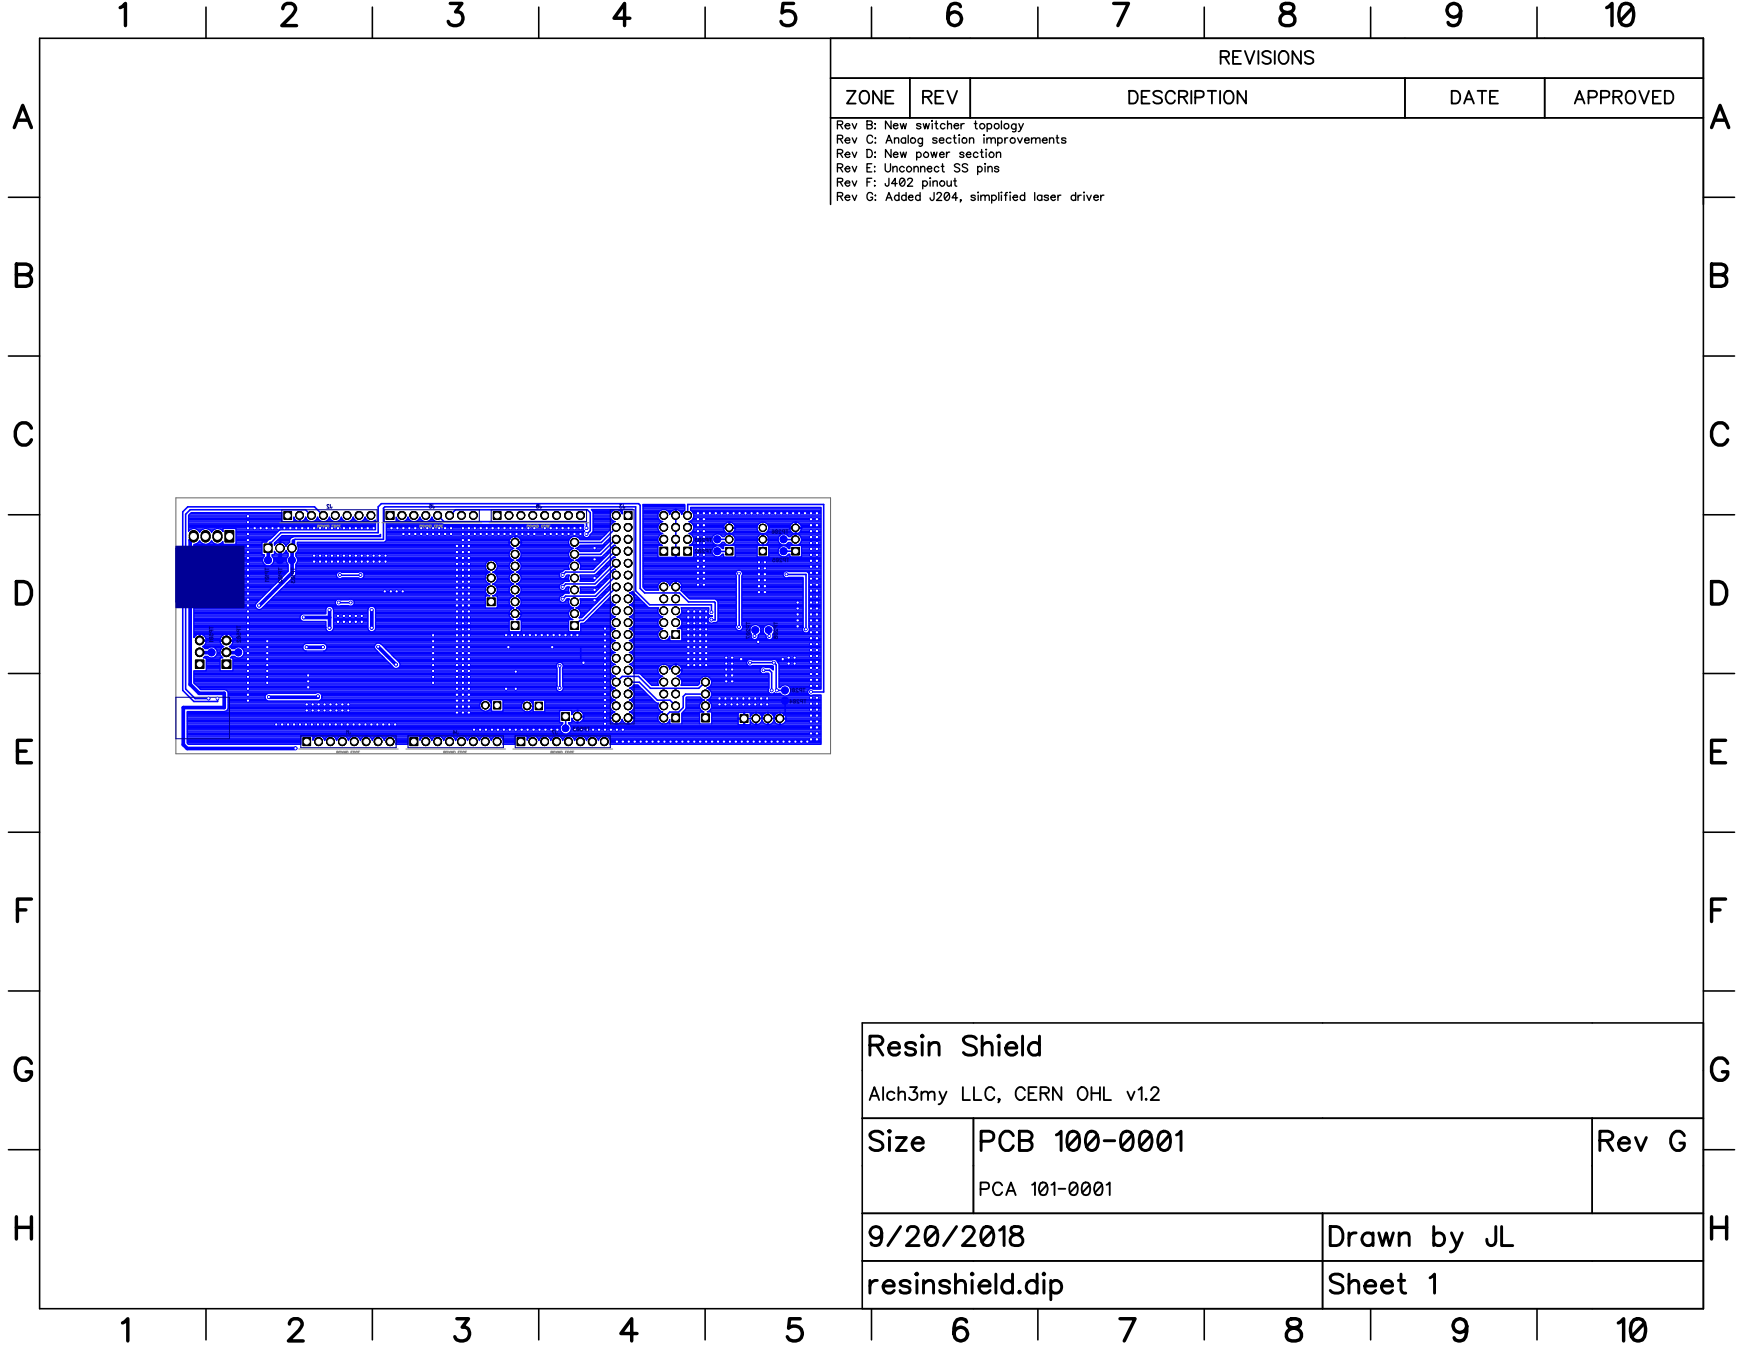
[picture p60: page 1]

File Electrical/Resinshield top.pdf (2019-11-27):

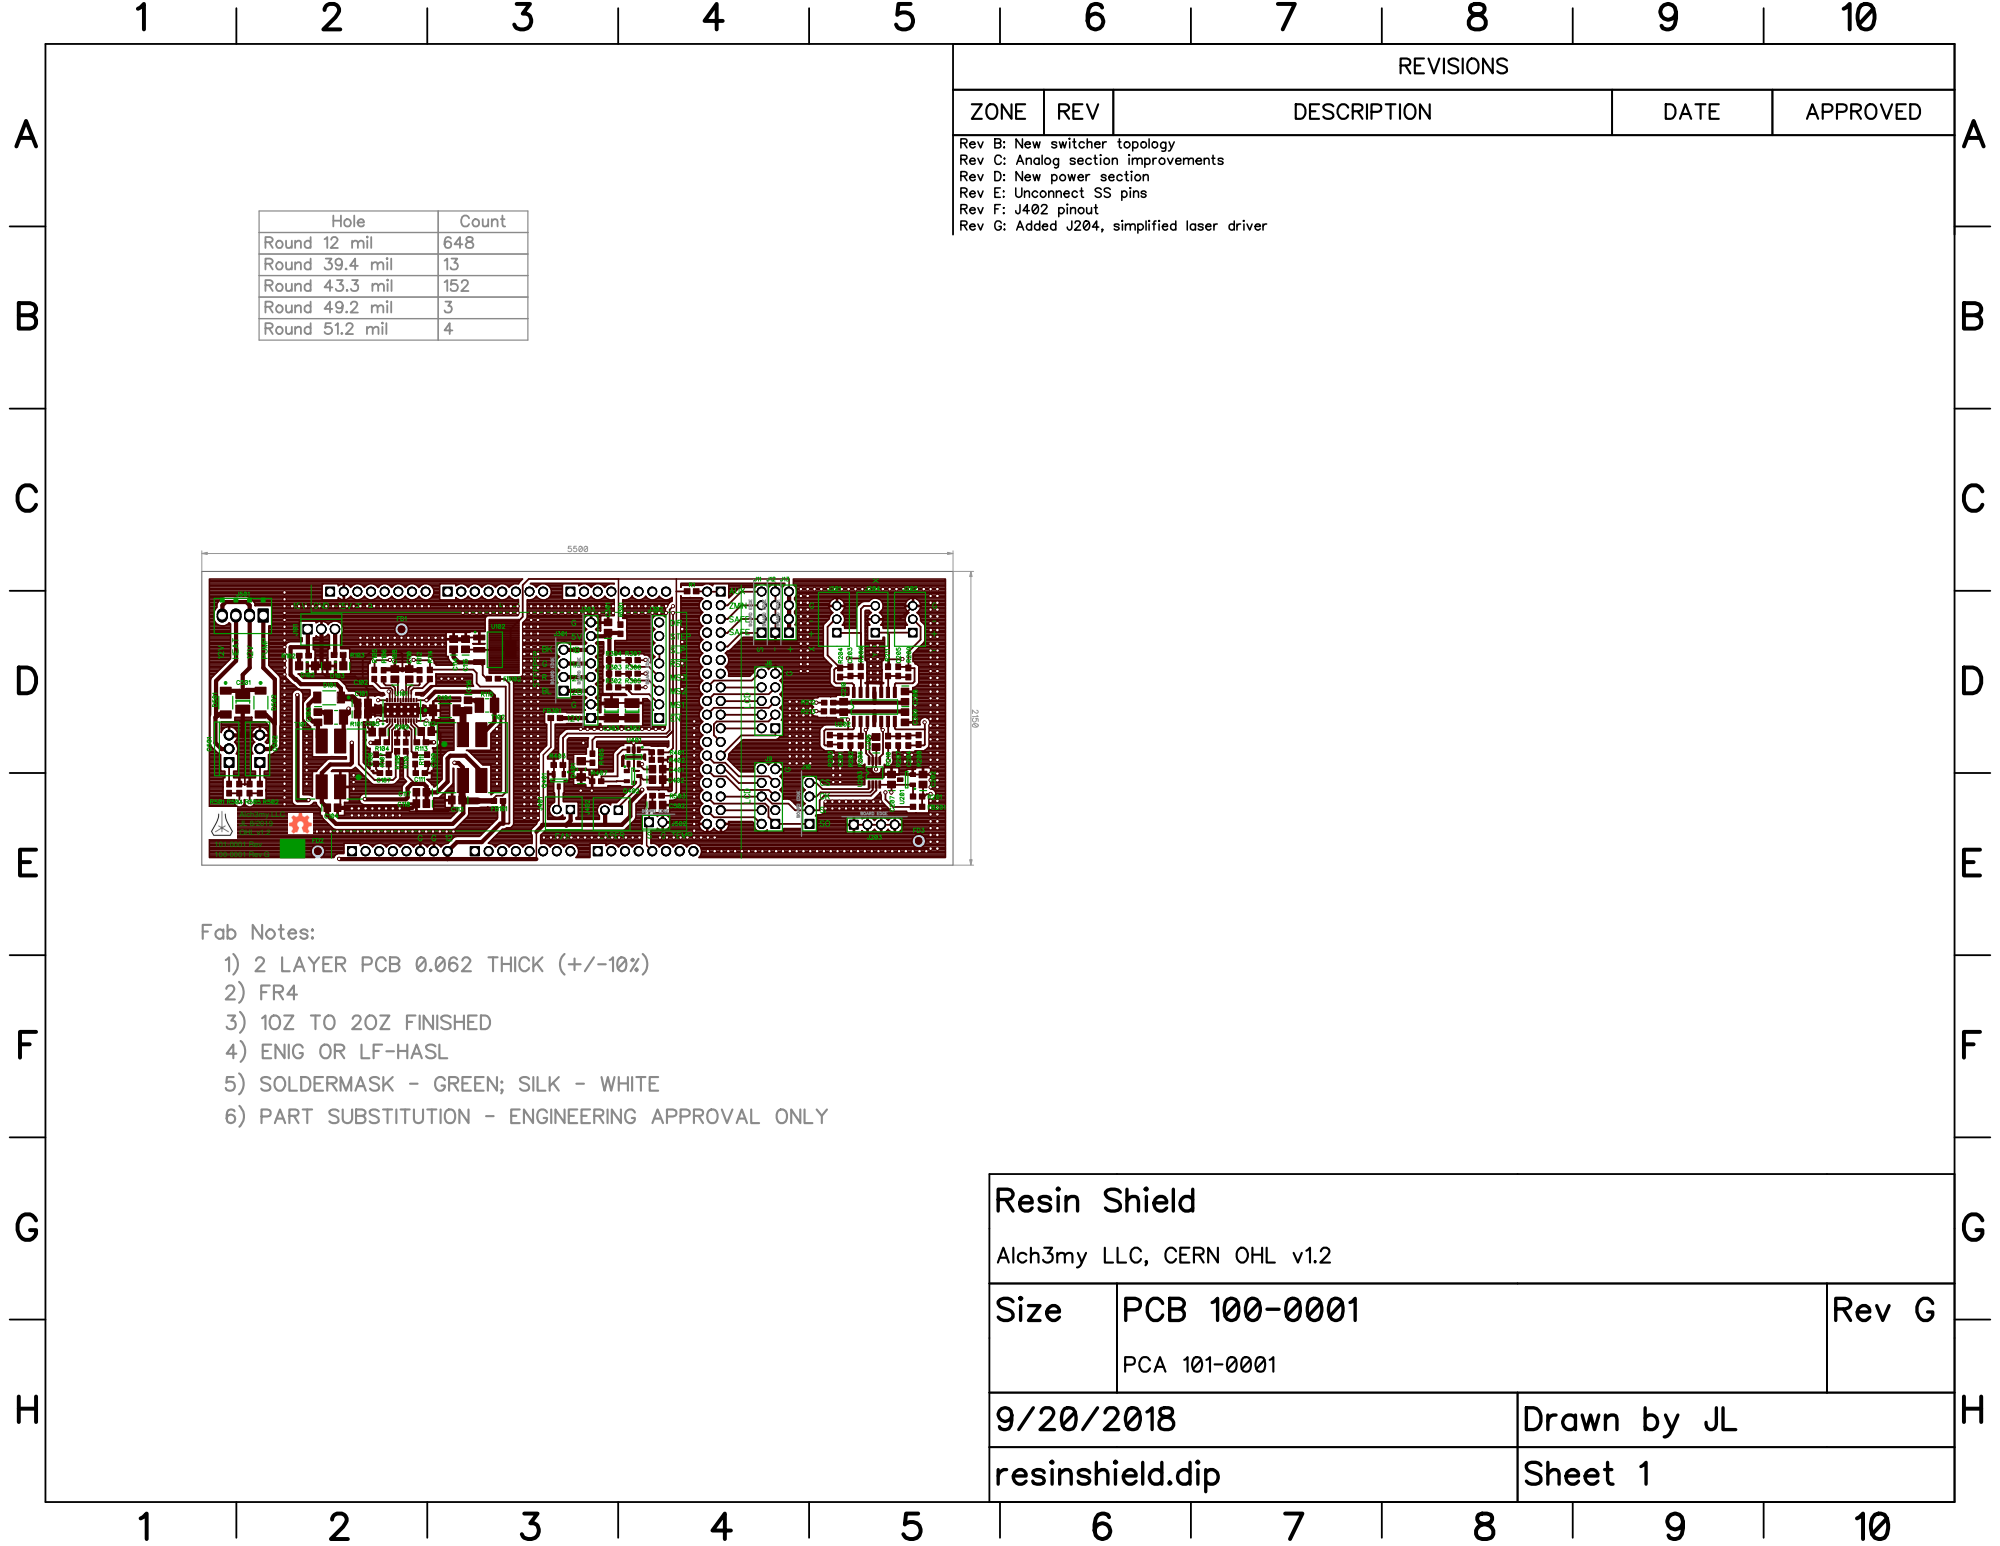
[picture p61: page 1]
100-0001 Rev G; 101-0001 Rev; OHL v1.2; Alch3my LLC JL 8/2019

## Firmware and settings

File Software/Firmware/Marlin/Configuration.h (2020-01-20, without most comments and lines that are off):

#define CONFIGURATION_H
#define CONFIGURATION_H_VERSION 010109
#define STRING_CONFIG_H_AUTHOR "(none, default config)" // Who made the changes.
#define SHOW_BOOTSCREEN
#define STRING_SPLASH_LINE1 SHORT_BUILD_VERSION // will be shown during bootup in line 1
#define STRING_SPLASH_LINE2 WEBSITE_URL         // will be shown during bootup in line 2
#define SERIAL_PORT 0
#define BAUDRATE 250000
  #define MOTHERBOARD BOARD_RESIN
#define BED_DIM                  120
#define RESIN_SEGMENTS_PER_SECOND 200
#define Z0_RESIN              168
#define R_RESIN               9    //New galvo = 7.76
#define EXTRUDERS 1
#define DEFAULT_NOMINAL_FILAMENT_DIA 3.0
#define POWER_SUPPLY 0
#define TEMP_SENSOR_0 1
#define TEMP_SENSOR_1 0
#define TEMP_SENSOR_2 0
#define TEMP_SENSOR_3 0
#define TEMP_SENSOR_4 0
#define TEMP_SENSOR_BED 0
#define TEMP_SENSOR_CHAMBER 0
#define DUMMY_THERMISTOR_998_VALUE 25
#define DUMMY_THERMISTOR_999_VALUE 100
#define MAX_REDUNDANT_TEMP_SENSOR_DIFF 10
#define TEMP_RESIDENCY_TIME 10  // (seconds)
#define TEMP_HYSTERESIS 3       // (degC) range of +/- temperatures considered "close" to the target one
#define TEMP_WINDOW     1       // (degC) Window around target to start the residency timer x degC early.
#define TEMP_BED_RESIDENCY_TIME 10  // (seconds)
#define TEMP_BED_HYSTERESIS 3       // (degC) range of +/- temperatures considered "close" to the target one
#define TEMP_BED_WINDOW     1       // (degC) Window around target to start the residency timer x degC early.
#define HEATER_0_MINTEMP 5
#define HEATER_1_MINTEMP 5
#define HEATER_2_MINTEMP 5
#define HEATER_3_MINTEMP 5
#define HEATER_4_MINTEMP 5
#define BED_MINTEMP 5
#define HEATER_0_MAXTEMP 275
#define HEATER_1_MAXTEMP 275
#define HEATER_2_MAXTEMP 275
#define HEATER_3_MAXTEMP 275
#define HEATER_4_MAXTEMP 275
#define BED_MAXTEMP 150
#define PIDTEMP
#define BANG_MAX 255     // Limits current to nozzle while in bang-bang mode; 255=full current
#define PID_MAX BANG_MAX // Limits current to nozzle while PID is active (see PID_FUNCTIONAL_RANGE below); 255=full current
#define PID_K1 0.95      // Smoothing factor within any PID loop
  #define PID_FUNCTIONAL_RANGE 10 // If the temperature difference between the target temperature and the actual temperature
  #define DEFAULT_Kp 22.2
  #define DEFAULT_Ki 1.08
  #define DEFAULT_Kd 114
#define MAX_BED_POWER 255 // limits duty cycle to bed; 255=full current
#define PREVENT_COLD_EXTRUSION
#define EXTRUDE_MINTEMP 30
#define PREVENT_LENGTHY_EXTRUDE
#define EXTRUDE_MAXLENGTH 200
#define THERMAL_PROTECTION_HOTENDS // Enable thermal protection for all extruders
#define THERMAL_PROTECTION_BED     // Enable thermal protection for the heated bed
#define USE_XMIN_PLUG
#define USE_YMIN_PLUG
#define USE_ZMIN_PLUG
#define ENDSTOPPULLUPS
#define X_MIN_ENDSTOP_INVERTING false // set to true to invert the logic of the endstop.
#define Y_MIN_ENDSTOP_INVERTING false // set to true to invert the logic of the endstop.
#define Z_MIN_ENDSTOP_INVERTING true // set to true to invert the logic of the endstop.
#define X_MAX_ENDSTOP_INVERTING false // set to true to invert the logic of the endstop.
#define Y_MAX_ENDSTOP_INVERTING false // set to true to invert the logic of the endstop.
#define Z_MAX_ENDSTOP_INVERTING false // set to true to invert the logic of the endstop.
#define Z_MIN_PROBE_ENDSTOP_INVERTING false // set to true to invert the logic of the probe.
#define X_DRIVER_TYPE  A4988
#define Y_DRIVER_TYPE  A4988
#define Z_DRIVER_TYPE  A4988
#define X2_DRIVER_TYPE A4988
#define Y2_DRIVER_TYPE A4988
#define Z2_DRIVER_TYPE A4988
#define E0_DRIVER_TYPE A4988
#define E1_DRIVER_TYPE A4988
#define E2_DRIVER_TYPE A4988
#define E3_DRIVER_TYPE A4988
#define E4_DRIVER_TYPE A4988
#define DEFAULT_AXIS_STEPS_PER_UNIT   {82964, 82964, 804, 4000} //{525, 525, 804, 4000} // AROUND 1448 //{525, 525, 804, 4000}
#define DEFAULT_MAX_FEEDRATE          { 32767, 32767, 2, 25 }
#define DEFAULT_MAX_ACCELERATION      { 300, 300, 50, 1000 }//{ 30000, 30000, 50, 1000 }
#define DEFAULT_ACCELERATION          30000    // X, Y, Z and E acceleration for printing moves
#define DEFAULT_RETRACT_ACCELERATION  300    // E acceleration for retracts
#define DEFAULT_TRAVEL_ACCELERATION   30000    // X, Y, Z acceleration for travel (non printing) moves
#define DEFAULT_XJERK                 300.0
#define DEFAULT_YJERK                 300.0
#define DEFAULT_ZJERK                  0.3
#define DEFAULT_EJERK                  5.0
#define Z_MIN_PROBE_USES_Z_MIN_ENDSTOP_PIN
#define X_PROBE_OFFSET_FROM_EXTRUDER 10  // X offset: -left  +right  [of the nozzle]
#define Y_PROBE_OFFSET_FROM_EXTRUDER 10  // Y offset: -front +behind [the nozzle]
#define Z_PROBE_OFFSET_FROM_EXTRUDER 0   // Z offset: -below +above  [the nozzle]
#define MIN_PROBE_EDGE 10
#define XY_PROBE_SPEED 8000
#define Z_PROBE_SPEED_FAST HOMING_FEEDRATE_Z
#define Z_PROBE_SPEED_SLOW (Z_PROBE_SPEED_FAST / 2)
#define Z_CLEARANCE_DEPLOY_PROBE   10 // Z Clearance for Deploy/Stow
#define Z_CLEARANCE_BETWEEN_PROBES  5 // Z Clearance between probe points
#define Z_CLEARANCE_MULTI_PROBE     5 // Z Clearance between multiple probes
#define Z_PROBE_LOW_POINT          -2 // Farthest distance below the trigger-point to go before stopping
#define Z_PROBE_OFFSET_RANGE_MIN -20
#define Z_PROBE_OFFSET_RANGE_MAX 20
#define X_ENABLE_ON 0
#define Y_ENABLE_ON 0
#define Z_ENABLE_ON 0
#define E_ENABLE_ON 0 // For all extruders
#define DISABLE_X false
#define DISABLE_Y false
#define DISABLE_Z false
#define DISABLE_E false // For all extruders
#define DISABLE_INACTIVE_EXTRUDER true // Keep only the active extruder enabled.
#define INVERT_X_DIR false
#define INVERT_Y_DIR false
#define INVERT_Z_DIR false
#define INVERT_E0_DIR false
#define INVERT_E1_DIR false
#define INVERT_E2_DIR false
#define INVERT_E3_DIR false
#define INVERT_E4_DIR false
#define X_HOME_DIR -1
#define Y_HOME_DIR -1
#define Z_HOME_DIR -1
#define X_BED_SIZE 120
#define Y_BED_SIZE 120
#define X_MIN_POS -1 * X_BED_SIZE / 2
#define Y_MIN_POS -1 * Y_BED_SIZE / 2
#define Z_MIN_POS 0
#define X_MAX_POS X_BED_SIZE / 2
#define Y_MAX_POS Y_BED_SIZE / 2
#define Z_MAX_POS 160
#define MIN_SOFTWARE_ENDSTOPS
  #define MIN_SOFTWARE_ENDSTOP_X
  #define MIN_SOFTWARE_ENDSTOP_Y
  #define MIN_SOFTWARE_ENDSTOP_Z
#define MAX_SOFTWARE_ENDSTOPS
  #define MAX_SOFTWARE_ENDSTOP_X
  #define MAX_SOFTWARE_ENDSTOP_Y
  #define MAX_SOFTWARE_ENDSTOP_Z
#define HOMING_FEEDRATE_XY (50*60)
#define HOMING_FEEDRATE_Z  (4*60)
#define EEPROM_CHITCHAT   // Give feedback on EEPROM commands. Disable to save PROGMEM.
#define HOST_KEEPALIVE_FEATURE        // Disable this if your host doesn't like keepalive messages
#define DEFAULT_KEEPALIVE_INTERVAL 2  // Number of seconds between "busy" messages. Set with M113.
#define BUSY_WHILE_HEATING            // Some hosts require "busy" messages even during heating
#define PREHEAT_1_TEMP_HOTEND 180
#define PREHEAT_1_TEMP_BED     70
#define PREHEAT_1_FAN_SPEED     0 // Value from 0 to 255
#define PREHEAT_2_TEMP_HOTEND 240
#define PREHEAT_2_TEMP_BED    110
#define PREHEAT_2_FAN_SPEED     0 // Value from 0 to 255
#define PRINTJOB_TIMER_AUTOSTART
#define LCD_LANGUAGE en
#define DISPLAY_CHARSET_HD44780 JAPANESE
#define SOFT_PWM_SCALE 0
#define SERVO_DELAY { 300 }

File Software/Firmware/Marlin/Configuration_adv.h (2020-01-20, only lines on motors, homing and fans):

#define E0_AUTO_FAN_PIN -1
#define E1_AUTO_FAN_PIN -1
#define E2_AUTO_FAN_PIN -1
#define E3_AUTO_FAN_PIN -1
#define E4_AUTO_FAN_PIN -1
#define CHAMBER_AUTO_FAN_PIN -1
#define X_HOME_BUMP_MM 5
#define Y_HOME_BUMP_MM 5
#define Z_HOME_BUMP_MM 2
#define HOMING_BUMP_DIVISOR { 2, 2, 4 }  // Re-Bump Speed Divisor (Divides the Homing Feedrate)
#define MICROSTEP_MODES { 16, 16, 16, 16, 16 } // [1,2,4,8,16]
#define DIGIPOT_I2C_MOTOR_CURRENTS { 1.0, 1.0, 1.0, 1.0, 1.0, 1.0, 1.0, 1.0 }  //  AZTEEG_X3_PRO

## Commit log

2019-11-27 Drawer and Frame instructions
2019-11-27 Frame is complete
2019-11-27 Added hardware source files
    [201-0001 Rev C bedsm.stp, 201-0002 Rev A3 reservoirsm.stp, 900-0001 Rev C0 LR3 ASM BOM.xlsx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]
2019-11-27 Added license info to individual files
    [clear_acrylic_p1.dxf, clear_orange_p1.dxf, clear_orange_p2.dxf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]
2020-01-20 firmware
    firmware
    [Configuration.h, Configuration_adv.h]
2020-01-20 added schematic

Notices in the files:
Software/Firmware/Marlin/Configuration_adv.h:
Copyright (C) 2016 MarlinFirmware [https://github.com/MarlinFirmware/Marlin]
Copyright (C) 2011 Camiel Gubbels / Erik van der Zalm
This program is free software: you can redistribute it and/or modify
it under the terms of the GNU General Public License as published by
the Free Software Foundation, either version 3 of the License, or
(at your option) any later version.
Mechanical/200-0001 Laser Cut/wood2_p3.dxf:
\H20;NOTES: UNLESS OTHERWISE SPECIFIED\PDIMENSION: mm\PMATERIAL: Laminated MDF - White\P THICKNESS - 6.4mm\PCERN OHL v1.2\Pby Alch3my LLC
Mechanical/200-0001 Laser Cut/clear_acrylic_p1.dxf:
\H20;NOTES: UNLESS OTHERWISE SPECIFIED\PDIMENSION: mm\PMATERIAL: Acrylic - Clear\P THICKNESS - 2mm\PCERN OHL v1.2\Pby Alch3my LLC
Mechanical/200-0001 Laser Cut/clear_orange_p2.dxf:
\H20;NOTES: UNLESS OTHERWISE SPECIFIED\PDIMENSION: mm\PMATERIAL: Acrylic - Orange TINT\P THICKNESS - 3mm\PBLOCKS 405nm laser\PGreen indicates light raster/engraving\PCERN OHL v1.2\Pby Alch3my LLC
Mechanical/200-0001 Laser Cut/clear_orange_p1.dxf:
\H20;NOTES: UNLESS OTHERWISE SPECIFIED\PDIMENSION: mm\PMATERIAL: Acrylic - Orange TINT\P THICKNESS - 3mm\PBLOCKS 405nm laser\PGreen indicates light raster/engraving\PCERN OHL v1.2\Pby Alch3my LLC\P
